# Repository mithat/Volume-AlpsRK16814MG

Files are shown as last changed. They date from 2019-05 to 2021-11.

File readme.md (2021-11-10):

Volume-AlpsRK16814MG
====================

_Because volume control is free and for the people.™_

Description
-----------
[KiCad 5.0](http://www.kicad.org) design files for a PCB that integrates an 
Alps RK16814MG motorized potentiometer with an H bridge to drive the motor
using logic-level signals.

### Inputs and outputs

| Name | Function  |
|---|---|
| `VOL_UP` | Logical input to rotate the potentiometer clockwise. |
| `VOL_DOWN` | Logical input to rotate the potentiometer counter-clockwise. |
| `V_MOT` | Power for motor drive. Nominally 6 VDC, but see comments below. |
| `+5VD` | Power for logic circuits. 5 VDC. |
| `DGND` | Ground for digital (logic) circuits. |
| `CHASSIS GROUND` | Ground for potentiometer case. Also labeled as C.G. on top side of PCB. |
| `A_TOP` | Potentiometer A input |
| `A_WIPER` | Potentiometer A output |
| `AB_COMMON` | Potentiometer A and B's common (typically connects to signal ground) |
| `B_TOP` | Potentiometer B input |
| `B_WIPER` | Potentiometer A output |
| `C_TOP` | Potentiometer C input |
| `C_WIPER` | Potentiometer C output |
| `CD_COMMON` | Potentiometer C and D's common (typically connects to signal ground) |
| `D_TOP` | Potentiometer D input |
| `D_WIPER` | Potentiometer D output |

### Power
There are two power inputs to the board, one for the 5 VDC logic (`+5VD`)
and the other to drive the potentiometer's motor (`V_MOT`). The board has a 
jumper (`J1`) that when installed will connect `V_MOT` to `+5VD`---making it
possible to operate the module from just one `+5VDC` power source, albeit with
a couple caveats.

First, owing to the voltage drop across the Darlington H-bridge, the optimum 
voltage for `V_MOT` is 6 VDC. When `V_MOT` is 5 VDC, the resulting voltage
delivered to the Alps RK16814MG's motor falls below Alps' specified minimum. 
However, the motor seems to have no problem operating at this lower than 
specified voltage. Second, the motor's maximum specified current consumption is 
150 mA. This is beyond the capacity of, for example, the on-board regulators
found on many Arduinos. Therefore, if you opt to jumper J1, you may have to use 
an external logic supply if you are using something like an Arduino for 
control.

### Grounding
The logic supply ground is completely isolated from other grounds. For the love 
of all  that is good, don't mix your logic and audio grounds. Connect the
logic and audio grounds at one point only and as close to the main power 
supplies as possible.

It is assumed the case of the potentiometer is grounded through the chassis. A
ground pin labeled `C.G.` is provided if this is not the case. This connection 
should not be used as a signal ground but rather only to provide a shielding 
connection for the potentiometer's case.

The potentiometer internally connects the "ground" sides of both elements of 
each gang. These are brought out as independent commons (`AB_COMMON` and 
`CD_COMMON`). Typically, `AB_COMMON` and `CD_COMMON` will be connected to 
signal ground.

### Use
While it's possible to use the **Volume-AlpsRK16814MG** PCB for applications 
other than volume control, we assume that you will be using it for volume 
control.

The Alps RK16814MG consists of two gangs of dual potentiometers. Refer to the
table above for the PCB's I/O corresponding to these.

For regular (non-differential) stereo use, you have the option of using both
elements of one gang (e.g., A and B) or one element from from each gang (e.g., 
A and C).

For differential stereo control, both elements on both gangs will be required.

To rotate the potentiometer CW (i.e., up), apply a logical 1 to `VOL_UP` and a
logical 0 to `VOL_DOWN`. To rotate the potentiometer CCW (i.e., down), apply a 
logical 1 to `VOL_DOWN` and a logical 0 to `VOL_UP`. No harm will come if a 
logical 1 is applied to both `VOL_UP` and `VOL_DOWN` simultaneously.

License
-------
CERN Open Hardware License v1.2 

Copyright
---------
Copyright (C) 2015 Mithat Konar.

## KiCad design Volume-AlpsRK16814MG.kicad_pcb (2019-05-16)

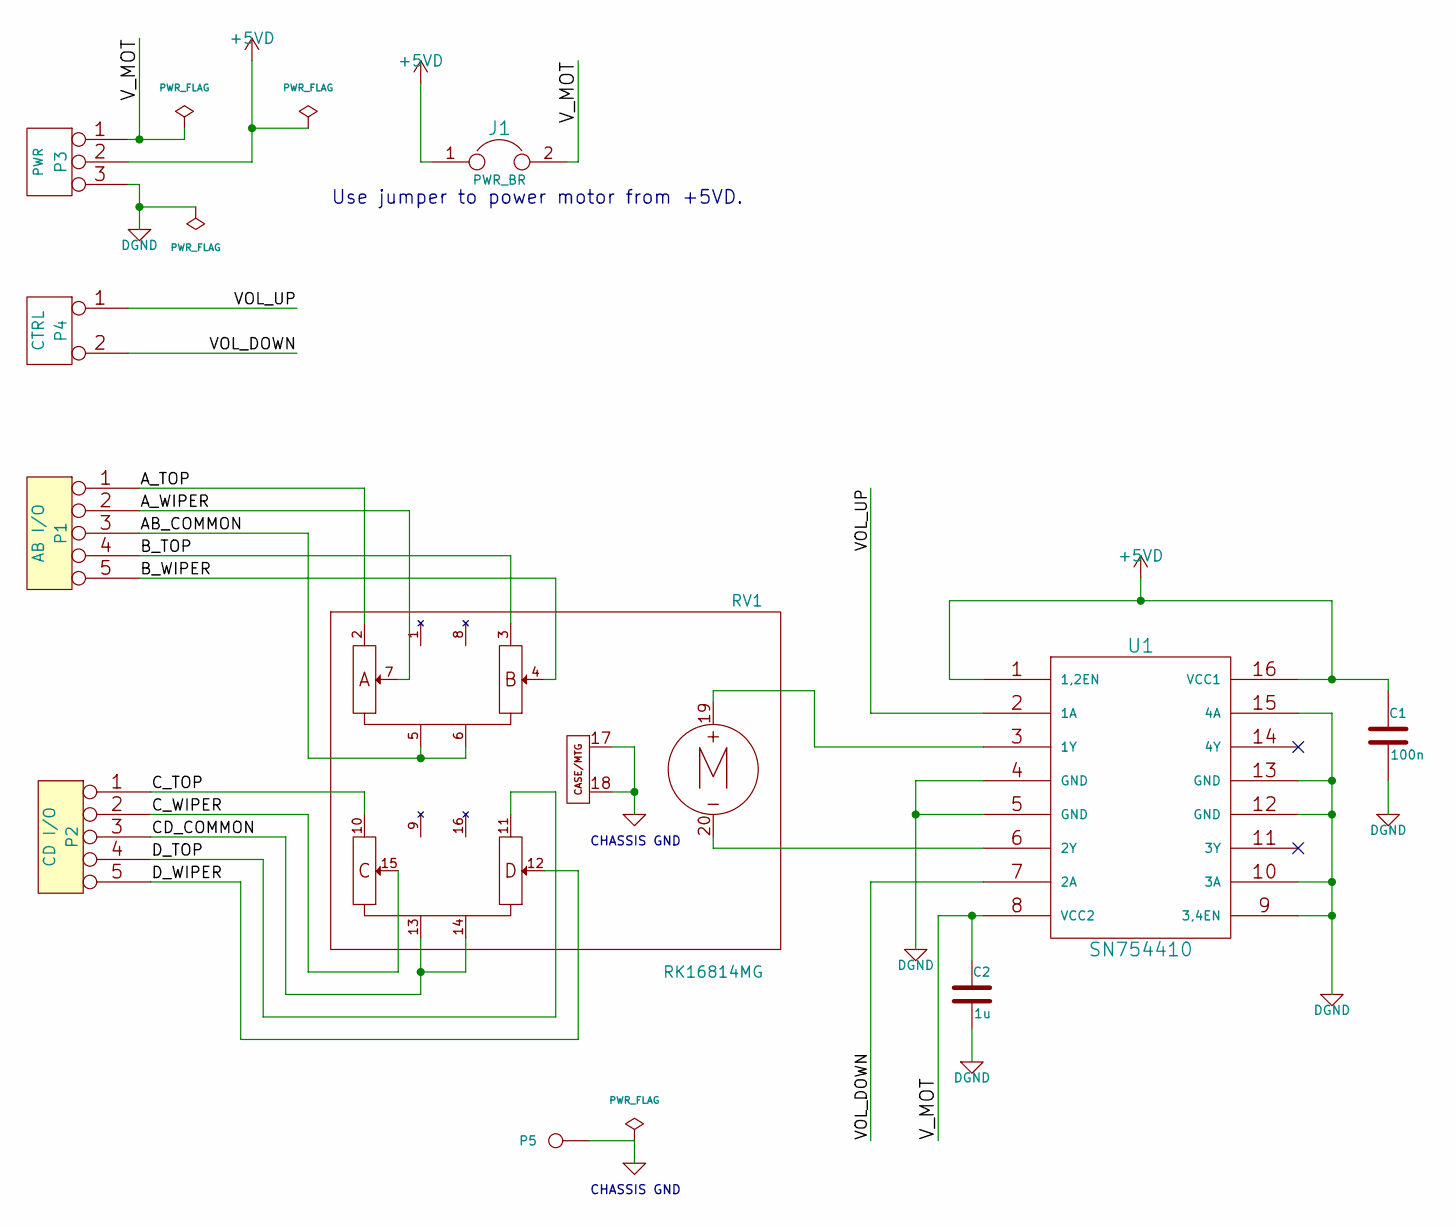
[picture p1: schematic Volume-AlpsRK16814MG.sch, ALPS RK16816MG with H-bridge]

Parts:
C1: 100n; C_4.0_2.5_2.5_0.5
C2: 1u; C_4.0_2.5_2.5_0.5
J1: PWR_BR; SIL-2
P1: AB I/O; TE_282834-5
P2: CD I/O; TE_282834-5
P3: PWR; TE_282834-3
P4: CTRL; TE_282834-2
P5: GND; AVA-20ga
RV1: RK16814MG; ALPS_RK16814MG
U1: SN754410; DIP-16_AriesC84_e

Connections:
+5VD: C1.1, J1.1, P3.2 (PM), U1.1 (1,2EN), U1.16 (VCC1)
/AB_COMMON: P1.3, RV1.5 (ABcommon), RV1.6 (ABcommon)
/A_TOP: P1.1, RV1.2 (A1)
/A_WIPER: P1.2, RV1.7 (A2)
/B_TOP: P1.4, RV1.3 (B1)
/B_WIPER: P1.5, RV1.4 (B2)
/CD_COMMON: P2.3, RV1.13 (CDcommon), RV1.14 (CDcommon)
/C_TOP: P2.1, RV1.10 (C1)
/C_WIPER: P2.2, RV1.15 (C2)
/D_TOP: P2.4, RV1.11 (D1)
/D_WIPER: P2.5, RV1.12 (D2)
/VOL_DOWN: P4.2 (PM), U1.7 (2A)
/VOL_UP: P4.1, U1.2 (1A)
/V_MOT: C2.1, J1.2, P3.1, U1.8 (VCC2)
DGND: C1.2, C2.2, P3.3, U1.4 (GND), U1.5 (GND), U1.9 (3,4EN), U1.10 (3A), U1.12 (GND), U1.13 (GND), U1.15 (4A)
GND: P5.1, RV1.17 (Case), RV1.18 (Case)
unnamed: RV1.19 (Vmotor+), U1.3 (1Y)
unnamed: RV1.20 (Vmotor-), U1.6 (2Y)

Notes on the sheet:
CHASSIS GND
Use jumper to power motor from +5VD.

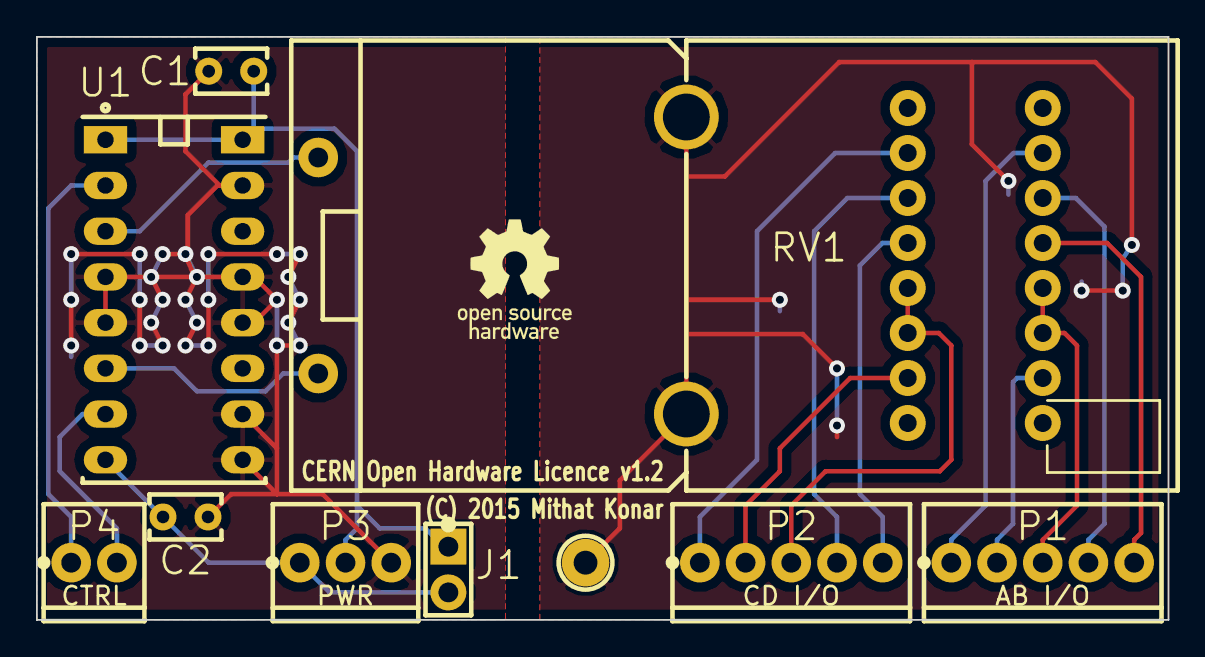
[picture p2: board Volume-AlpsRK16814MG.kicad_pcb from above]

Board: 2 copper layers, 62.9 x 32.4 mm, 12 parts (1 on the bottom side), 18 nets.

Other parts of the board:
LOGO1: REF; oshw-logo-250mil-FSilk
LOGO2: REF; oshw-logo-notext-100mil-FSilk

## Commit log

2015-03-21 Initial commit. Pre-route.
    [Volume-AlpsRK16814MG.kicad_pcb, Volume-AlpsRK16814MG.sch]
2015-03-21 Added bypass C to VCC2.
    [Volume-AlpsRK16814MG.kicad_pcb, Volume-AlpsRK16814MG.sch]
2015-03-22 Added cap to VCC2. Stitched SN754410 GND for heat.
    [Volume-AlpsRK16814MG.kicad_pcb]
2015-03-22 Added (C) and other additional labels silkscreen.
    [Volume-AlpsRK16814MG.kicad_pcb]
2015-03-23 Schematic presentation tweak.
    [Volume-AlpsRK16814MG.sch]
2015-03-27 Silkscreen optimizations. Added license to silkscreen.
    [Volume-AlpsRK16814MG.kicad_pcb, Volume-AlpsRK16814MG.sch]
2015-04-03 Silk tweaks.
    [Volume-AlpsRK16814MG.kicad_pcb]
2015-04-03 Schematic changes for independent motor drive voltage.
    [Volume-AlpsRK16814MG.sch]
2015-04-04 Added jumper to connect motor and digital supplies to schematic; PCB updated.
    [Volume-AlpsRK16814MG.kicad_pcb, Volume-AlpsRK16814MG.sch]
2015-04-04 .gitignore ignores top-level zip, png, and svg files. Added docs dir.
    [Volume-AlpsRK16814MG.kicad_pcb, Volume-AlpsRK16814MG.sch]
2015-04-09 Changed labels on PCB and schematic so names are consistent. Readme tweak.
    [Volume-AlpsRK16814MG.kicad_pcb, Volume-AlpsRK16814MG.sch]
2019-05-13 Schematic updated to KiCad 5.
    [Volume-AlpsRK16814MG-2019-05-12-18-40-09.sch, Volume-AlpsRK16814MG.kicad_pcb]
2019-05-14 Initial changes for converting PCB to KiCad 5.
    [Volume-AlpsRK16814MG.kicad_pcb, Volume-AlpsRK16814MG.sch]
2019-05-14 Silk changes.
    [Volume-AlpsRK16814MG.kicad_pcb]
2019-05-14 Update readme with KiCad version info.
2019-05-15 Moved footprints into local archive.
    [Volume-AlpsRK16814MG.kicad_pcb, Volume-AlpsRK16814MG.sch]
2019-05-16 Minor silkscreen adjustment.
    [Volume-AlpsRK16814MG.kicad_pcb]
2021-11-10 Update readme.md
    https://forum.kicad.info/t/warning-avoid-all-links-to-kicad-pcb-org-use-kicad-org/31521

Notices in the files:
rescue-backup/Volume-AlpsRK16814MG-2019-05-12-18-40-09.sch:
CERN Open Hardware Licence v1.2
